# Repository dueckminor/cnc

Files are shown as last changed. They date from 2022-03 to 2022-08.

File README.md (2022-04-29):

# CNC-Mill

This is my first try to build a CNC-Mill

As a controller I use an ESP-32 with
[FluidNC](https://github.com/bdring/FluidNC)

I designed a PCB with the following features:
- 4 stepper motors (for the X1,X2,Y,Z axes)
- 1 spindle output (enable+pwm)
- 5 additional output pins
- 8 limit switches (5V powered), 2 for each axis
- 1 probe switch
- 3 additional input pins
- 1 SD-Card
- 1 I2C (for an OLED display)

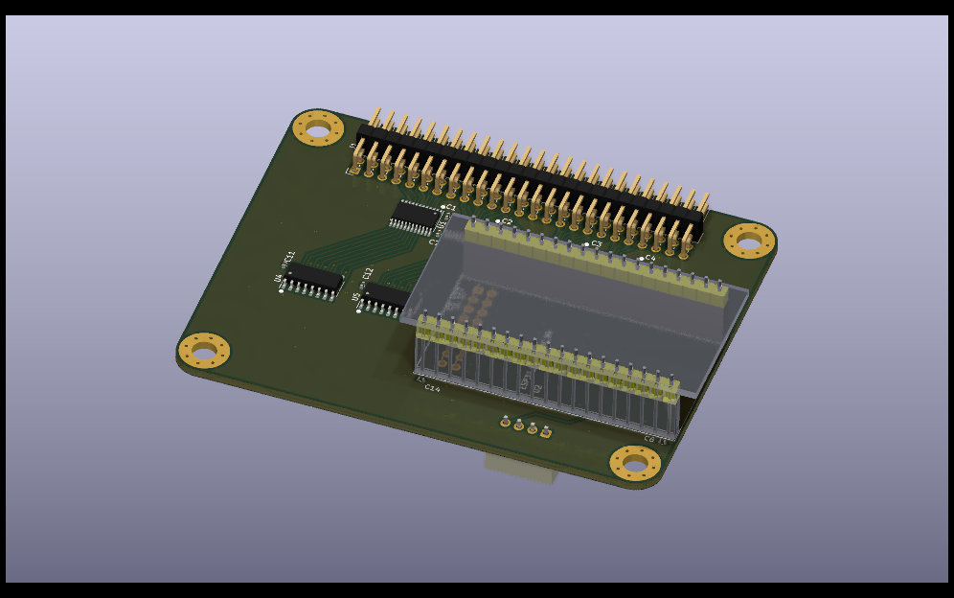
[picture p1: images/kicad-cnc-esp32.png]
esp32


This board gets connected using a 2x25 pin header to a connector-board
with many JST-XH connectors. This board contians also pull-up resistors
for each input switch (all inputs are active-low)

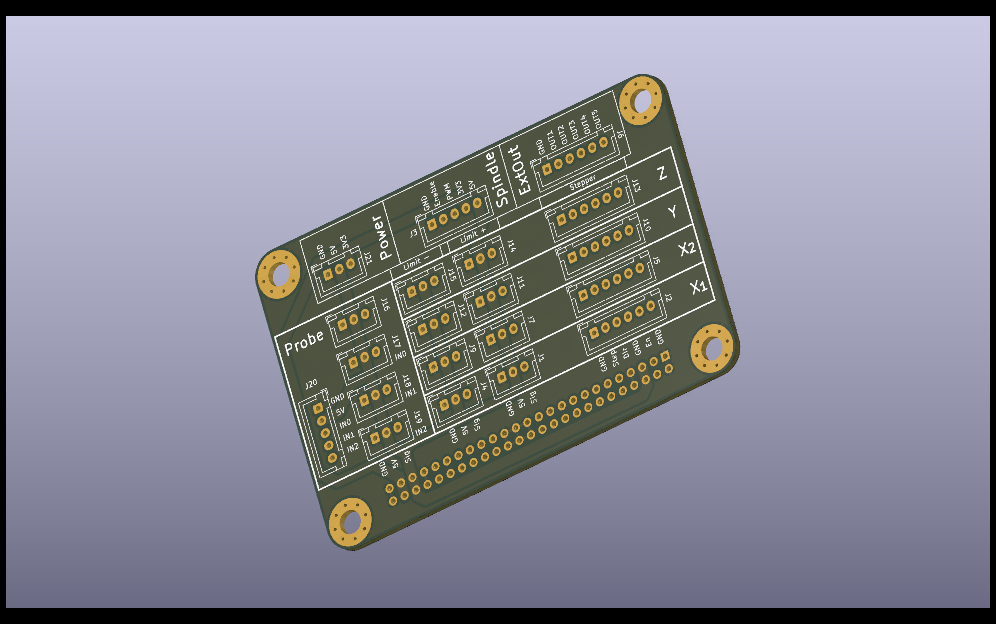
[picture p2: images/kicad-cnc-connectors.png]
connectors


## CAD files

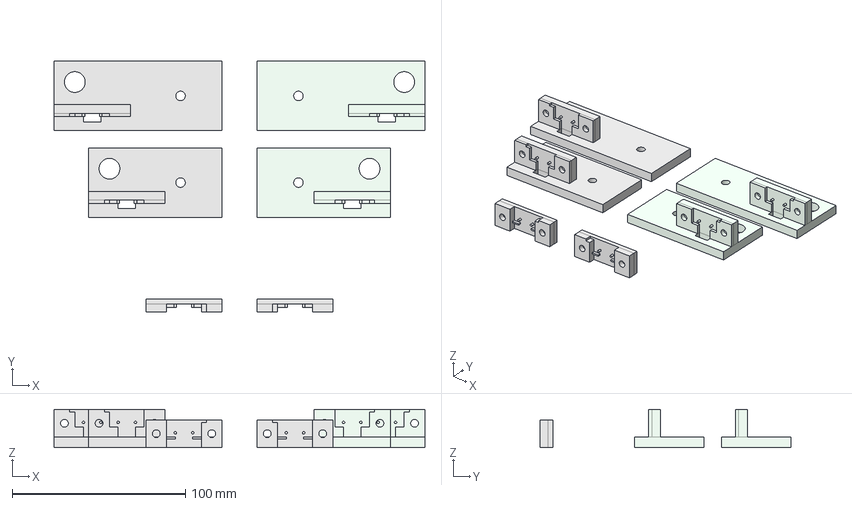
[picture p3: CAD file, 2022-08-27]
freecad/Endschalter-Halter.FCStd
214.0 x 144.5 x 22.0 mm
Halter-Kurz
Halter-Lang
Klemme
Halter-Kurz (Mirror #2)
Klemme (Mirror #3)
Halter-Lang (Mirror #3)

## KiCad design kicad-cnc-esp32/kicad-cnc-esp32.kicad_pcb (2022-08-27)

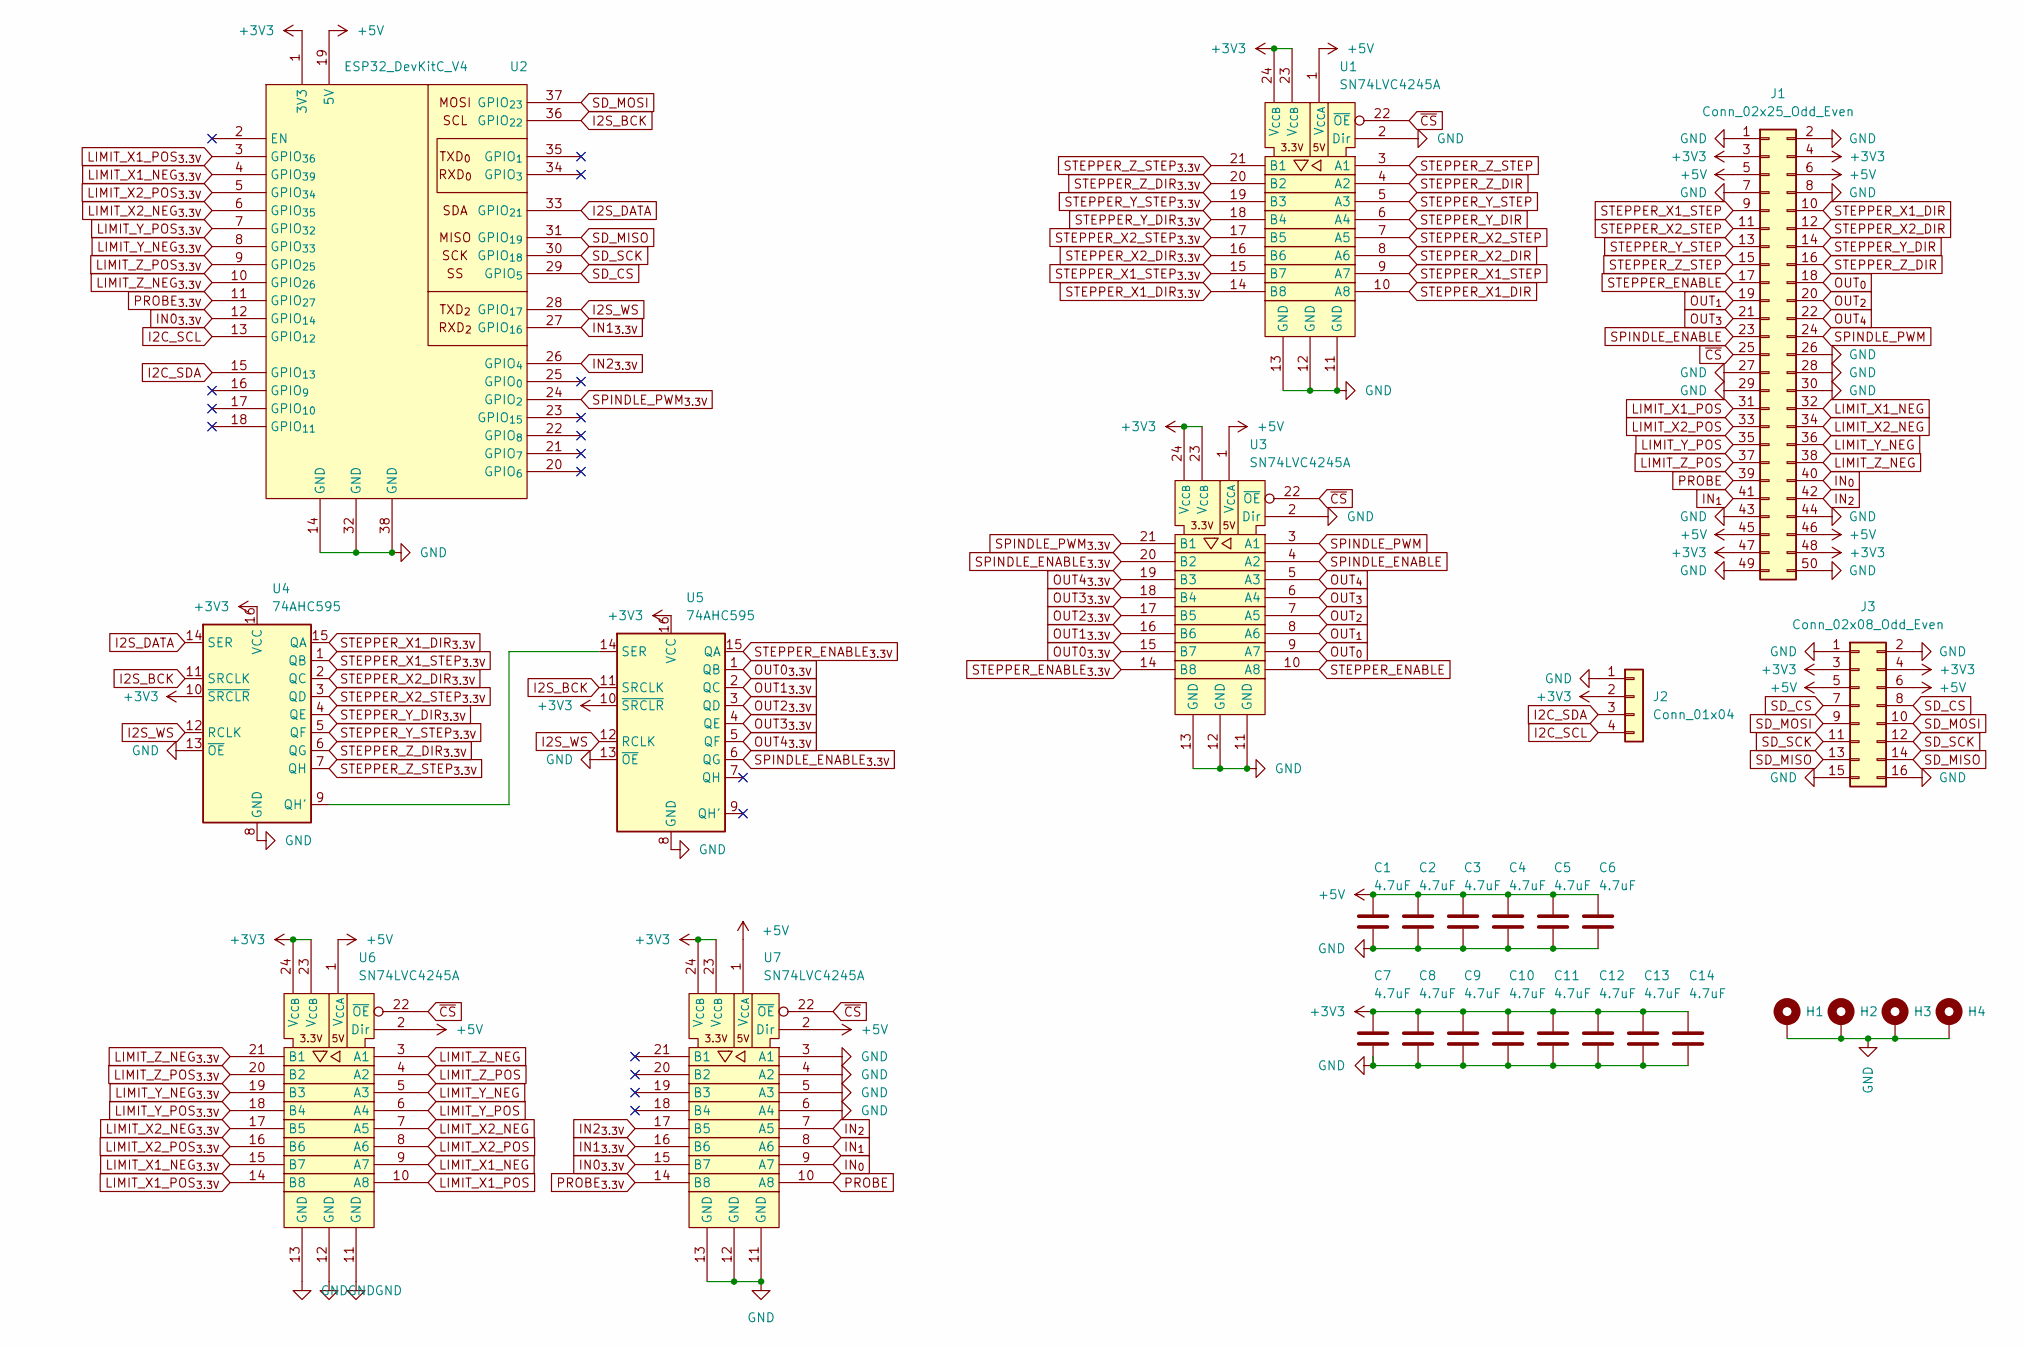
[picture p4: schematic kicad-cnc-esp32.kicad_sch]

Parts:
C1, C2, C3, C4, C5, C6, C7, C8, C9, C10, C11, C12, C13, C14: 4.7uF; C_0402_1005Metric; JLCPCB C23733
H1, H2, H3, H4: MountingHole_Pad; MountingHole_4.5mm_Pad_Via
J1: Conn_02x25_Odd_Even; PinHeader_2x25_P2.54mm_Horizontal
J2: Conn_01x04; JST_XH_B4B-XH-A_1x04_P2.50mm_Vertical
J3: Conn_02x08_Odd_Even; PinSocket_2x08_P2.54mm_Vertical
U1, U3, U6, U7: SN74LVC4245A; TSSOP-24_4.4x7.8mm_P0.65mm; JLCPCB C7859
U2: ESP32_DevKitC_V4
U4, U5: 74AHC595; SOIC-16_3.9x9.9mm_P1.27mm; JLCPCB C5947

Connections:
+3V3: C7.1, C8.1, C9.1, C10.1, C11.1, C12.1, C13.1, C14.1, J1.3, J1.4, J1.47, J1.48, J2.2, J3.3, J3.4, U1.23 (V_{CCB}), U1.24 (V_{CCB}), U2.1 (3V3), U3.23 (V_{CCB}), U3.24 (V_{CCB}), U4.10 (~SRCLR), U4.16 (VCC), U5.10 (~SRCLR), U5.16 (VCC), U6.23 (V_{CCB}), U6.24 (V_{CCB}), U7.23 (V_{CCB}), U7.24 (V_{CCB})
+5V: C1.1, C2.1, C3.1, C4.1, C5.1, C6.1, J1.5, J1.6, J1.45, J1.46, J3.5, J3.6, U1.1 (V_{CCA}), U2.19 (5V), U3.1 (V_{CCA}), U6.1 (V_{CCA}), U6.2 (Dir), U7.1 (V_{CCA}), U7.2 (Dir)
GND: C1.2, C2.2, C3.2, C4.2, C5.2, C6.2, C7.2, C8.2, C9.2, C10.2, C11.2, C12.2, C13.2, C14.2, H1.1, H2.1, H3.1, H4.1, J1.1, J1.2, J1.7, J1.8, J1.26, J1.27, J1.28, J1.29, J1.30, J1.43, J1.44, J1.49, J1.50, J2.1, J3.1, J3.2, J3.15, J3.16, U1.2 (Dir), U1.11 (GND), U1.12 (GND), U1.13 (GND), U2.14 (GND), U2.32 (GND), U2.38 (GND), U3.2 (Dir), U3.11 (GND), U3.12 (GND), U3.13 (GND), U4.8 (GND), U4.13 (~OE), U5.8 (GND), U5.13 (~OE), U6.11 (GND), U6.12 (GND), U6.13 (GND), U7.3 (A1), U7.4 (A2), U7.5 (A3), U7.6 (A4), U7.11 (GND), U7.12 (GND), U7.13 (GND)
I2C_SCL: J2.4, U2.13 (GPIO_{12})
I2C_SDA: J2.3, U2.15 (GPIO_{13})
I2S_BCK: U2.36 (GPIO_{22}), U4.11 (SRCLK), U5.11 (SRCLK)
I2S_DATA: U2.33 (GPIO_{21}), U4.14 (SER)
I2S_WS: U2.28 (GPIO_{17}), U4.12 (RCLK), U5.12 (RCLK)
IN0_{3.3V}: U2.12 (GPIO_{14}), U7.15 (B7)
IN1_{3.3V}: U2.27 (GPIO_{16}), U7.16 (B6)
IN2_{3.3V}: U2.26 (GPIO_{4}), U7.17 (B5)
IN_{0}: J1.40, U7.9 (A7)
IN_{1}: J1.41, U7.8 (A6)
IN_{2}: J1.42, U7.7 (A5)
LIMIT_X1_NEG: J1.32, U6.9 (A7)
LIMIT_X1_NEG_{3.3V}: U2.4 (GPIO_{39}), U6.15 (B7)
LIMIT_X1_POS: J1.31, U6.10 (A8)
LIMIT_X1_POS_{3.3V}: U2.3 (GPIO_{36}), U6.14 (B8)
LIMIT_X2_NEG: J1.34, U6.7 (A5)
LIMIT_X2_NEG_{3.3V}: U2.6 (GPIO_{35}), U6.17 (B5)
LIMIT_X2_POS: J1.33, U6.8 (A6)
LIMIT_X2_POS_{3.3V}: U2.5 (GPIO_{34}), U6.16 (B6)
LIMIT_Y_NEG: J1.36, U6.5 (A3)
LIMIT_Y_NEG_{3.3V}: U2.8 (GPIO_{33}), U6.19 (B3)
LIMIT_Y_POS: J1.35, U6.6 (A4)
LIMIT_Y_POS_{3.3V}: U2.7 (GPIO_{32}), U6.18 (B4)
LIMIT_Z_NEG: J1.38, U6.3 (A1)
LIMIT_Z_NEG_{3.3V}: U2.10 (GPIO_{26}), U6.21 (B1)
LIMIT_Z_POS: J1.37, U6.4 (A2)
LIMIT_Z_POS_{3.3V}: U2.9 (GPIO_{25}), U6.20 (B2)
unnamed: U4.9 (QH'), U5.14 (SER)
OUT0_{3.3V}: U3.15 (B7), U5.1 (QB)
OUT1_{3.3V}: U3.16 (B6), U5.2 (QC)
OUT2_{3.3V}: U3.17 (B5), U5.3 (QD)
OUT3_{3.3V}: U3.18 (B4), U5.4 (QE)
OUT4_{3.3V}: U3.19 (B3), U5.5 (QF)
OUT_{0}: J1.18, U3.9 (A7)
OUT_{1}: J1.19, U3.8 (A6)
OUT_{2}: J1.20, U3.7 (A5)
OUT_{3}: J1.21, U3.6 (A4)
OUT_{4}: J1.22, U3.5 (A3)
PROBE: J1.39, U7.10 (A8)
PROBE_{3.3V}: U2.11 (GPIO_{27}), U7.14 (B8)
SD_CS: J3.7, J3.8, U2.29 (GPIO_{5})
SD_MISO: J3.13, J3.14, U2.31 (GPIO_{19})
SD_MOSI: J3.9, J3.10, U2.37 (GPIO_{23})
SD_SCK: J3.11, J3.12, U2.30 (GPIO_{18})
SPINDLE_ENABLE: J1.23, U3.4 (A2)
SPINDLE_ENABLE_{3.3V}: U3.20 (B2), U5.6 (QG)
SPINDLE_PWM: J1.24, U3.3 (A1)
SPINDLE_PWM_{3.3V}: U2.24 (GPIO_{2}), U3.21 (B1)
STEPPER_ENABLE: J1.17, U3.10 (A8)
STEPPER_ENABLE_{3.3V}: U3.14 (B8), U5.15 (QA)
STEPPER_X1_DIR: J1.10, U1.10 (A8)
STEPPER_X1_DIR_{3.3V}: U1.14 (B8), U4.15 (QA)
STEPPER_X1_STEP: J1.9, U1.9 (A7)
STEPPER_X1_STEP_{3.3V}: U1.15 (B7), U4.1 (QB)
STEPPER_X2_DIR: J1.12, U1.8 (A6)
STEPPER_X2_DIR_{3.3V}: U1.16 (B6), U4.2 (QC)
STEPPER_X2_STEP: J1.11, U1.7 (A5)
STEPPER_X2_STEP_{3.3V}: U1.17 (B5), U4.3 (QD)
STEPPER_Y_DIR: J1.14, U1.6 (A4)
STEPPER_Y_DIR_{3.3V}: U1.18 (B4), U4.4 (QE)
STEPPER_Y_STEP: J1.13, U1.5 (A3)
STEPPER_Y_STEP_{3.3V}: U1.19 (B3), U4.5 (QF)
STEPPER_Z_DIR: J1.16, U1.4 (A2)
STEPPER_Z_DIR_{3.3V}: U1.20 (B2), U4.6 (QG)
STEPPER_Z_STEP: J1.15, U1.3 (A1)
STEPPER_Z_STEP_{3.3V}: U1.21 (B1), U4.7 (QH)
~CS: J1.25, U1.22 (~OE), U3.22 (~OE), U6.22 (~OE), U7.22 (~OE)

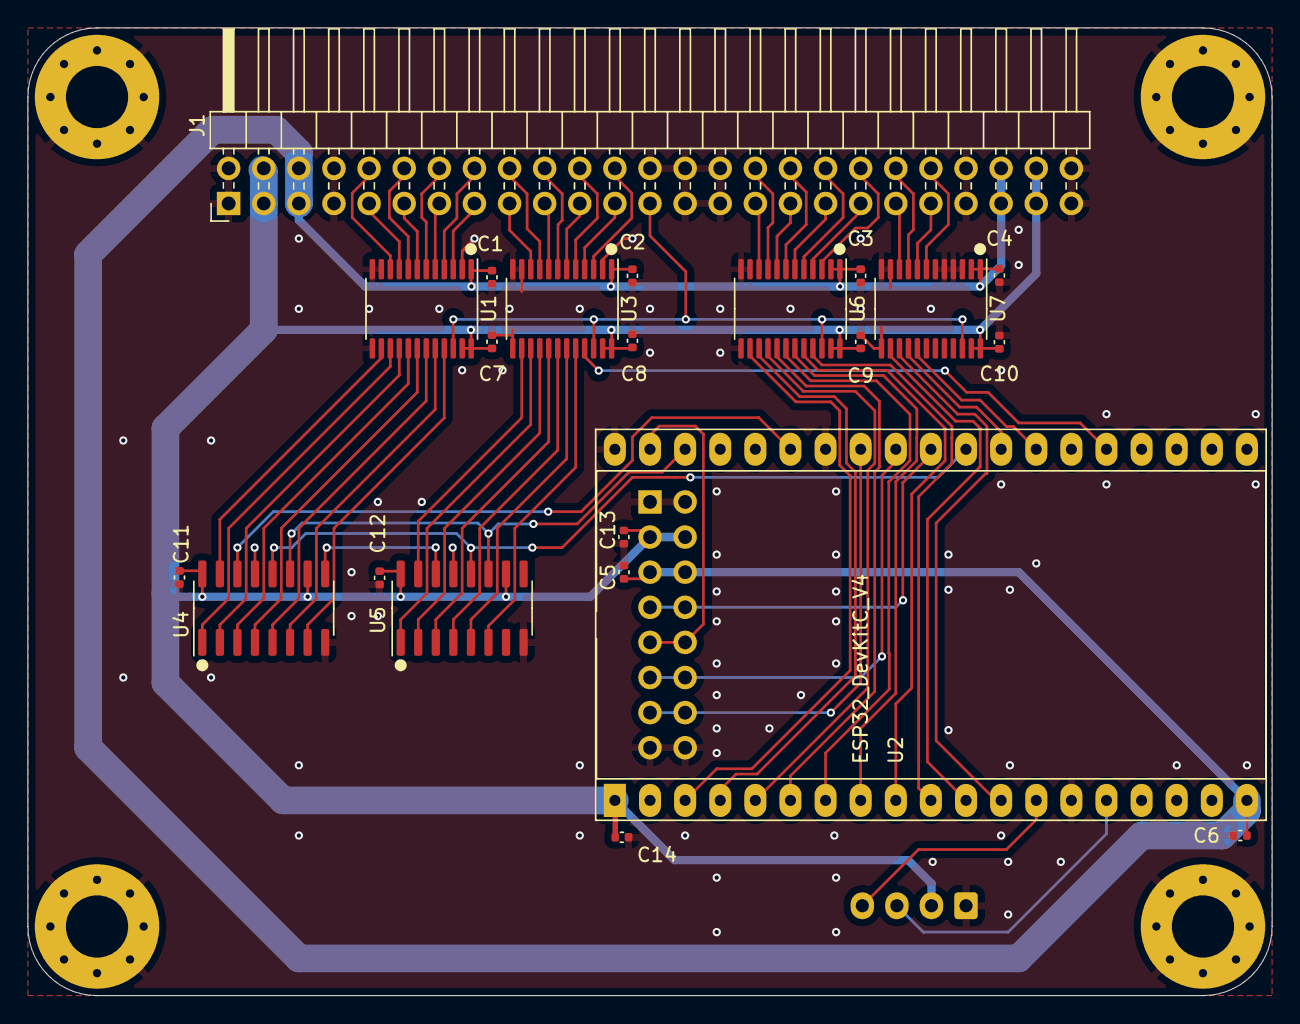
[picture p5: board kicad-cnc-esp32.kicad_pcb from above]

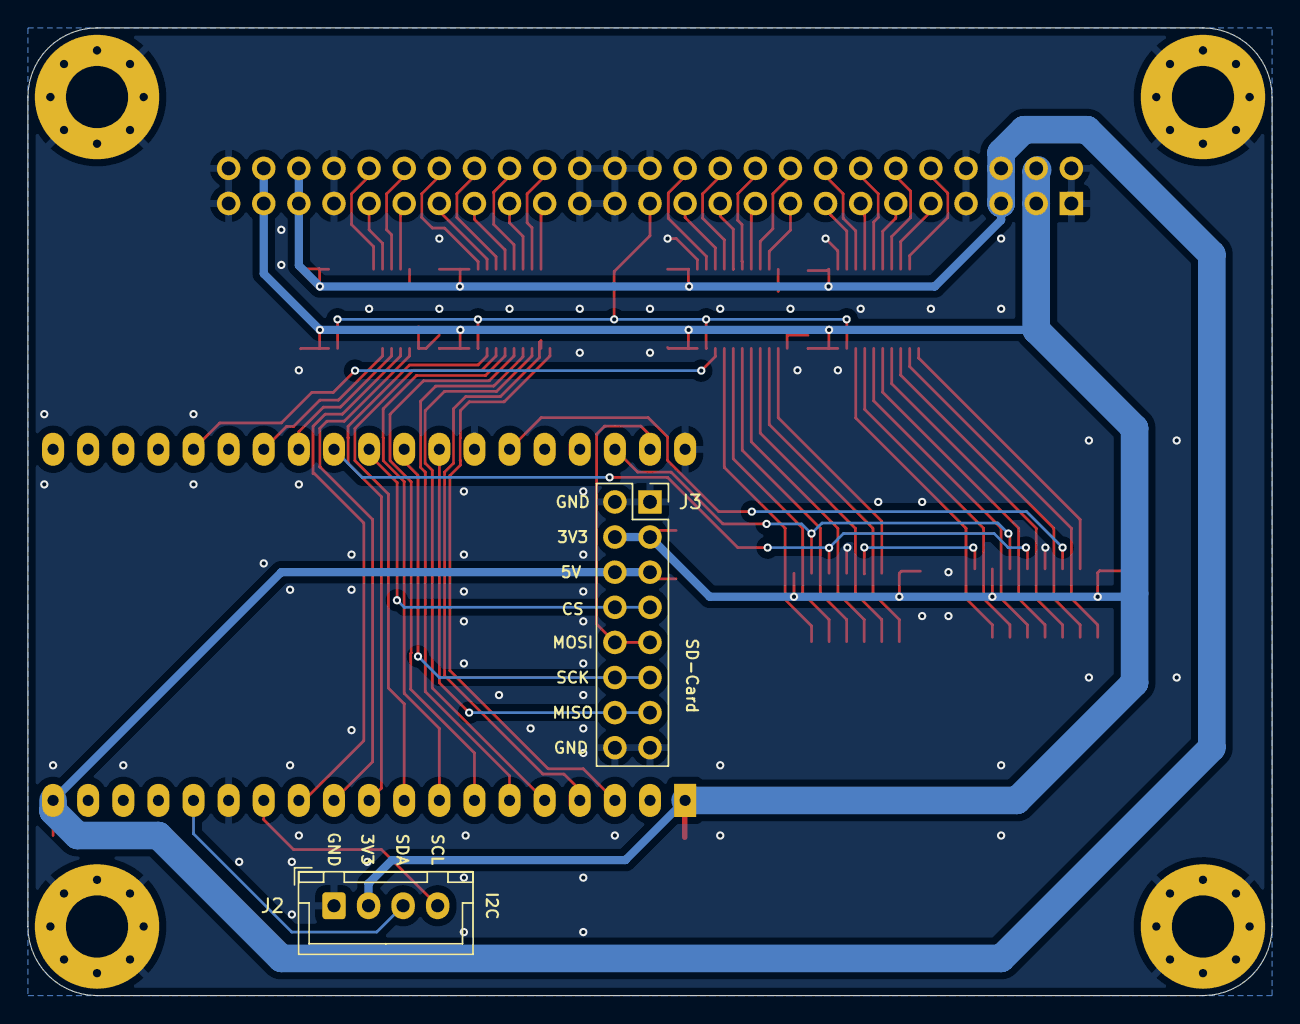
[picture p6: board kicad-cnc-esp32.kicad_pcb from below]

Board: 2 copper layers, 90.0 x 70.0 mm, 28 parts (2 on the bottom side), 70 nets.

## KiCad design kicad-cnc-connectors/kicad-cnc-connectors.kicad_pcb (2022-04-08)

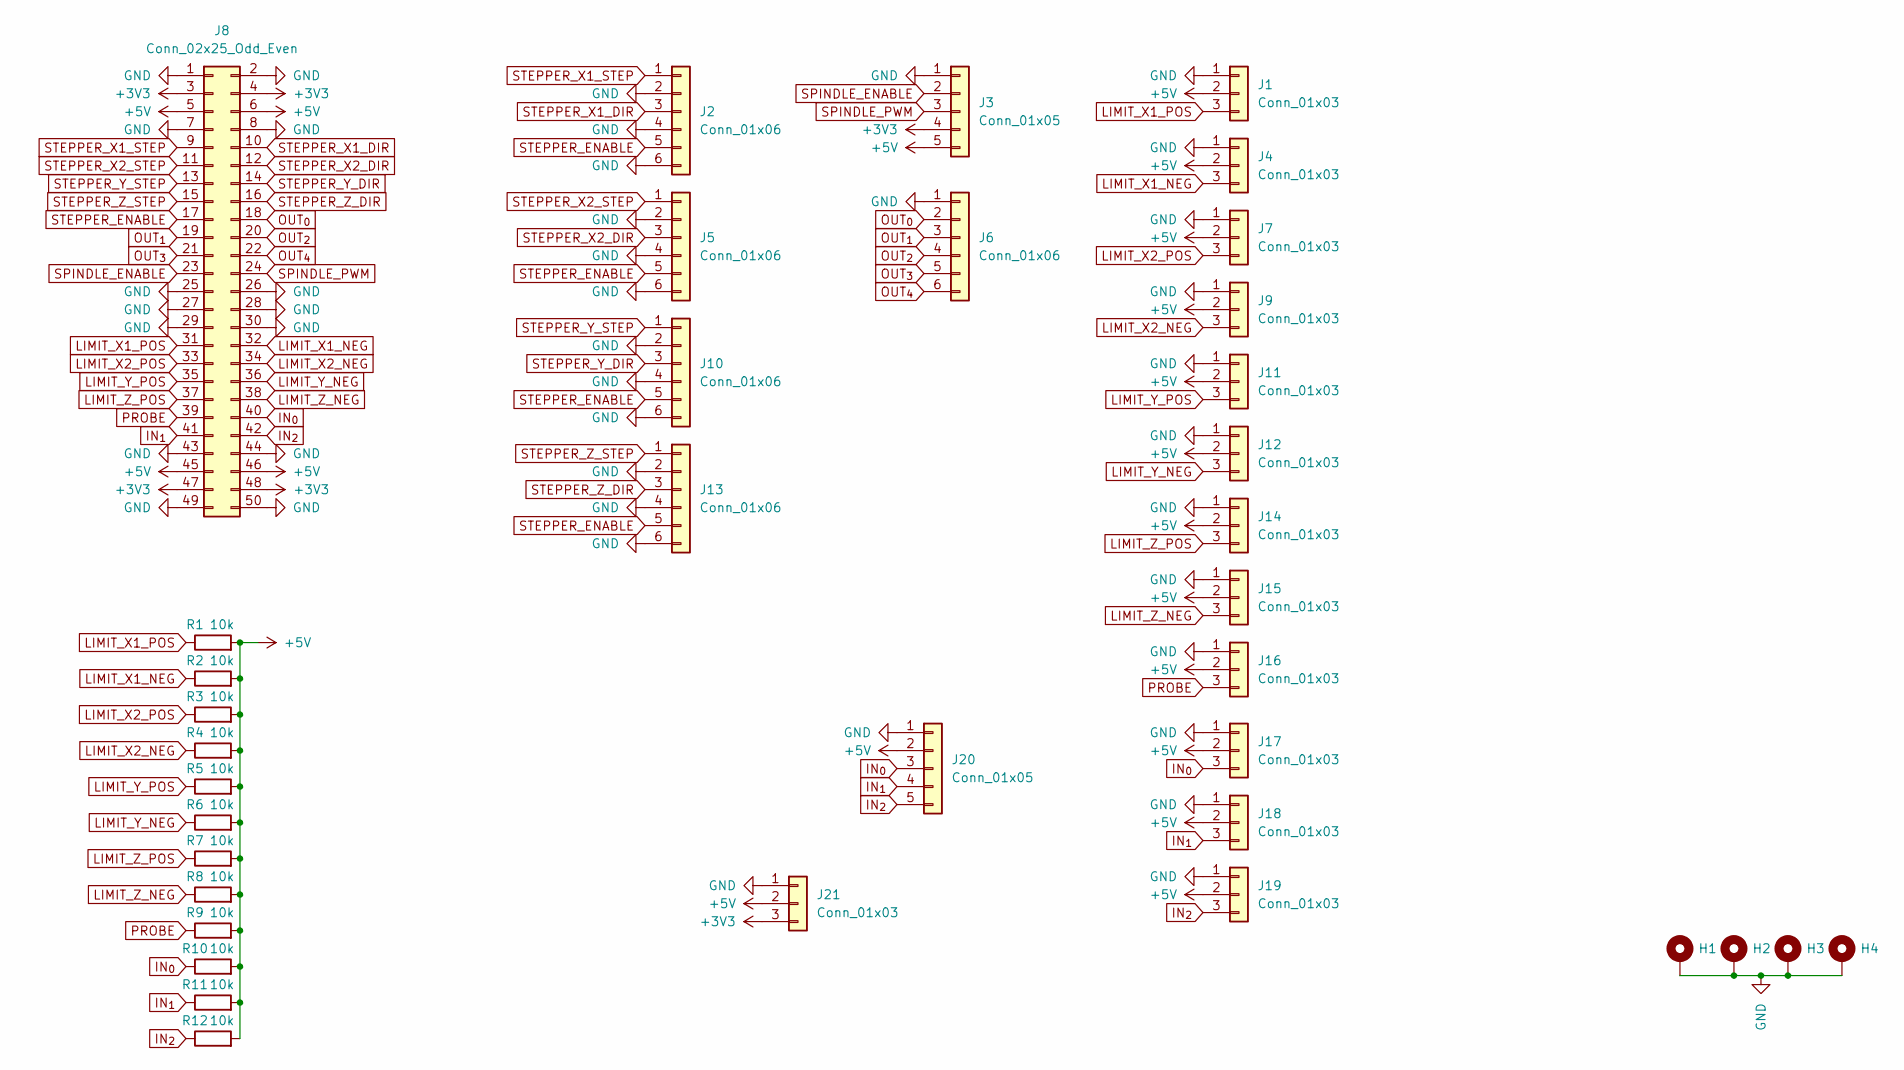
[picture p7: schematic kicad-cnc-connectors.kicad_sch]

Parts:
H1, H2, H3, H4: MountingHole_Pad; MountingHole_4.5mm_Pad_Via
J1, J4, J7, J9, J11, J12, J14, J15, J16, J17, J18, J19, J21: Conn_01x03; JST_XH_B3B-XH-A_1x03_P2.50mm_Vertical
J2, J5, J6, J10, J13: Conn_01x06; JST_XH_B6B-XH-A_1x06_P2.50mm_Vertical
J3, J20: Conn_01x05; JST_XH_B5B-XH-A_1x05_P2.50mm_Vertical
J8: Conn_02x25_Odd_Even; PinSocket_2x25_P2.54mm_Vertical
R1, R2, R3, R4, R5, R6, R7, R8, R9, R10, R11, R12: 10k; R_0402_1005Metric

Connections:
+3V3: J3.4, J8.3, J8.4, J8.47, J8.48, J21.3
+5V: J1.2, J3.5, J4.2, J7.2, J8.5, J8.6, J8.45, J8.46, J9.2, J11.2, J12.2, J14.2, J15.2, J16.2, J17.2, J18.2, J19.2, J20.2, J21.2, R1.2, R2.2, R3.2, R4.2, R5.2, R6.2, R7.2, R8.2, R9.2, R10.2, R11.2, R12.2
GND: H1.1, H2.1, H3.1, H4.1, J1.1, J2.2, J2.4, J2.6, J3.1, J4.1, J5.2, J5.4, J5.6, J6.1, J7.1, J8.1, J8.2, J8.7, J8.8, J8.25, J8.26, J8.27, J8.28, J8.29, J8.30, J8.43, J8.44, J8.49, J8.50, J9.1, J10.2, J10.4, J10.6, J11.1, J12.1, J13.2, J13.4, J13.6, J14.1, J15.1, J16.1, J17.1, J18.1, J19.1, J20.1, J21.1
IN_{0}: J8.40, J17.3, J20.3, R10.1
IN_{1}: J8.41, J18.3, J20.4, R11.1
IN_{2}: J8.42, J19.3, J20.5, R12.1
LIMIT_X1_NEG: J4.3, J8.32, R2.1
LIMIT_X1_POS: J1.3, J8.31, R1.1
LIMIT_X2_NEG: J8.34, J9.3, R4.1
LIMIT_X2_POS: J7.3, J8.33, R3.1
LIMIT_Y_NEG: J8.36, J12.3, R6.1
LIMIT_Y_POS: J8.35, J11.3, R5.1
LIMIT_Z_NEG: J8.38, J15.3, R8.1
LIMIT_Z_POS: J8.37, J14.3, R7.1
OUT_{0}: J6.2, J8.18
OUT_{1}: J6.3, J8.19
OUT_{2}: J6.4, J8.20
OUT_{3}: J6.5, J8.21
OUT_{4}: J6.6, J8.22
PROBE: J8.39, J16.3, R9.1
SPINDLE_ENABLE: J3.2, J8.23
SPINDLE_PWM: J3.3, J8.24
STEPPER_ENABLE: J2.5, J5.5, J8.17, J10.5, J13.5
STEPPER_X1_DIR: J2.3, J8.10
STEPPER_X1_STEP: J2.1, J8.9
STEPPER_X2_DIR: J5.3, J8.12
STEPPER_X2_STEP: J5.1, J8.11
STEPPER_Y_DIR: J8.14, J10.3
STEPPER_Y_STEP: J8.13, J10.1
STEPPER_Z_DIR: J8.16, J13.3
STEPPER_Z_STEP: J8.15, J13.1

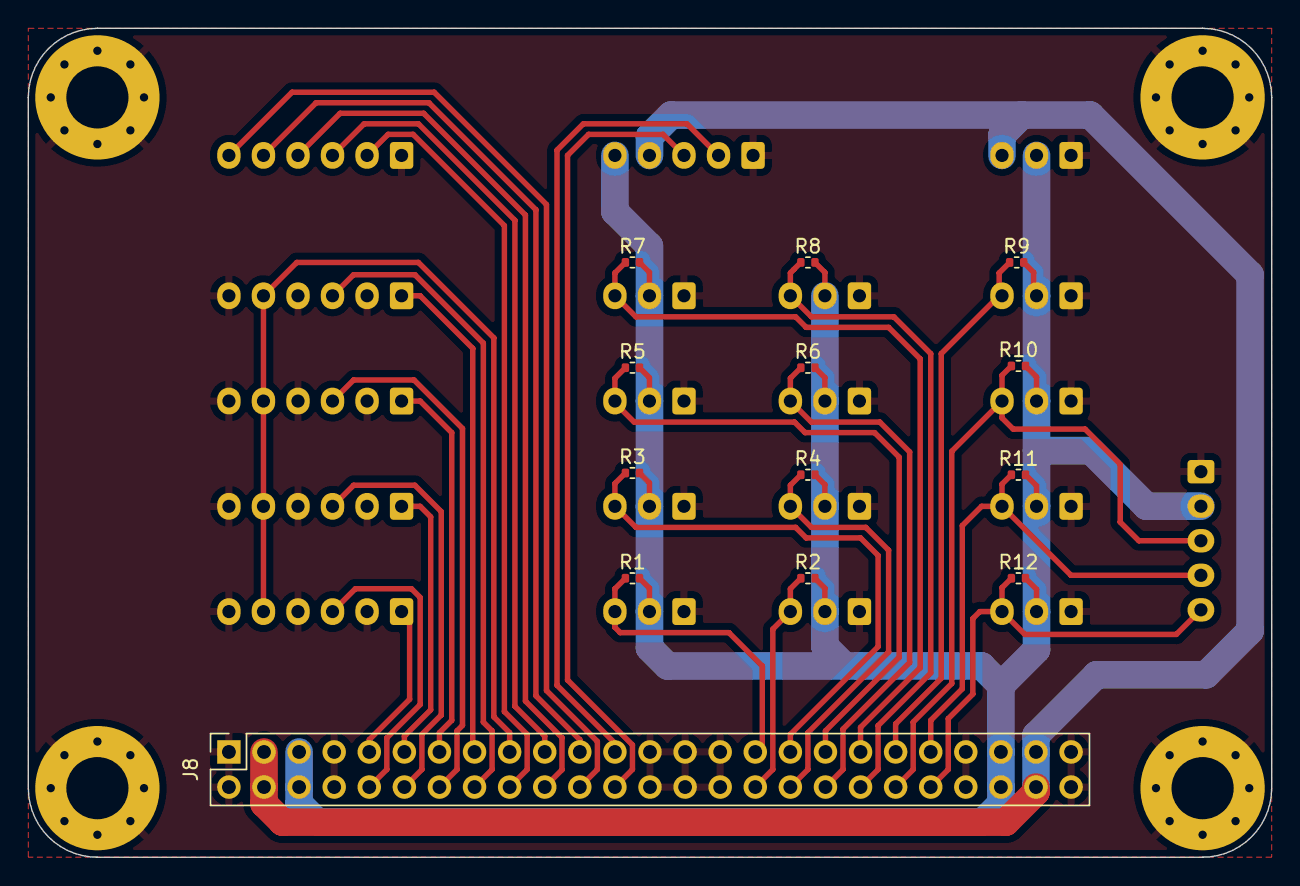
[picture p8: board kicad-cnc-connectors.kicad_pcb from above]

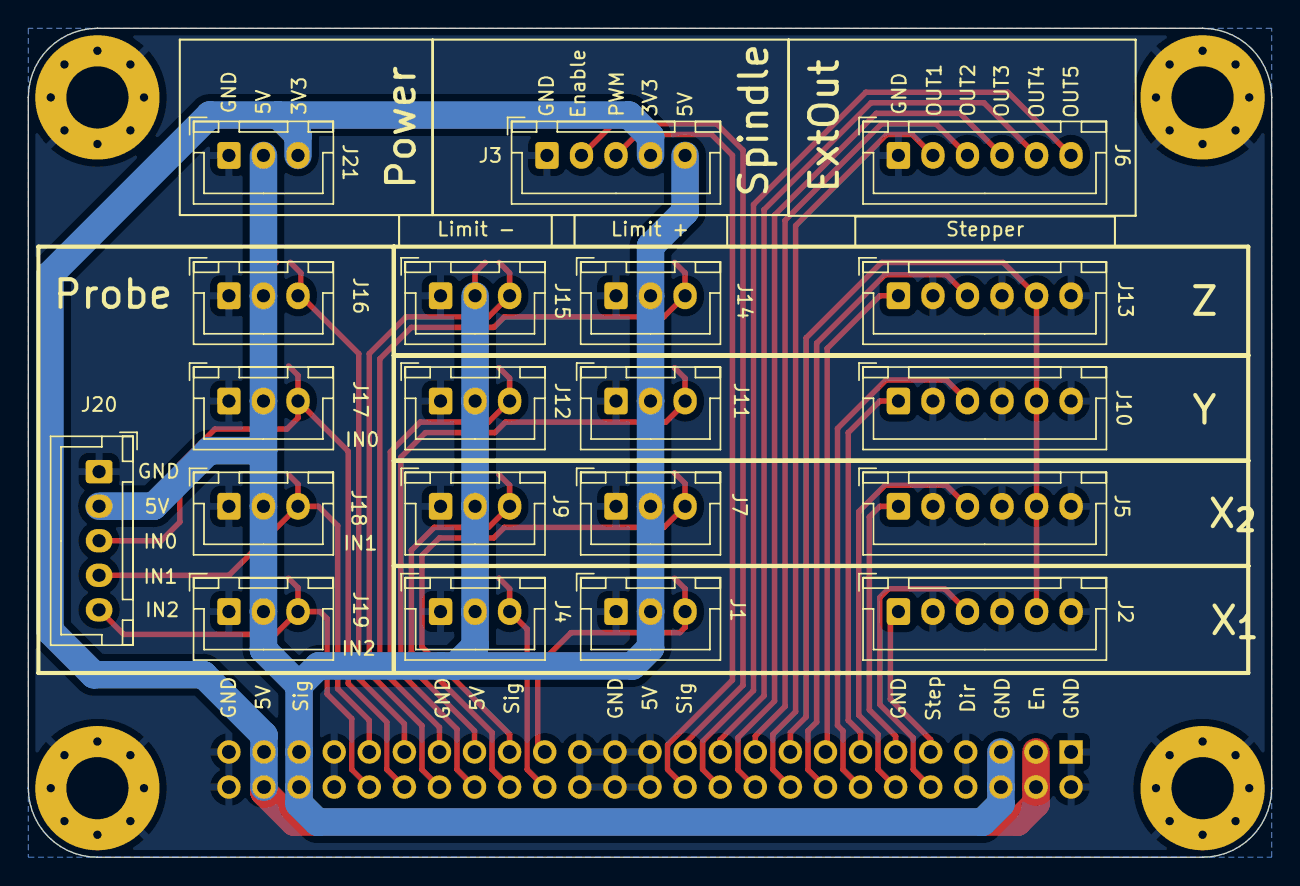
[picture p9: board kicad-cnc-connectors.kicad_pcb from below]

Board: 2 copper layers, 90.0 x 60.0 mm, 37 parts (20 on the bottom side), 31 nets.

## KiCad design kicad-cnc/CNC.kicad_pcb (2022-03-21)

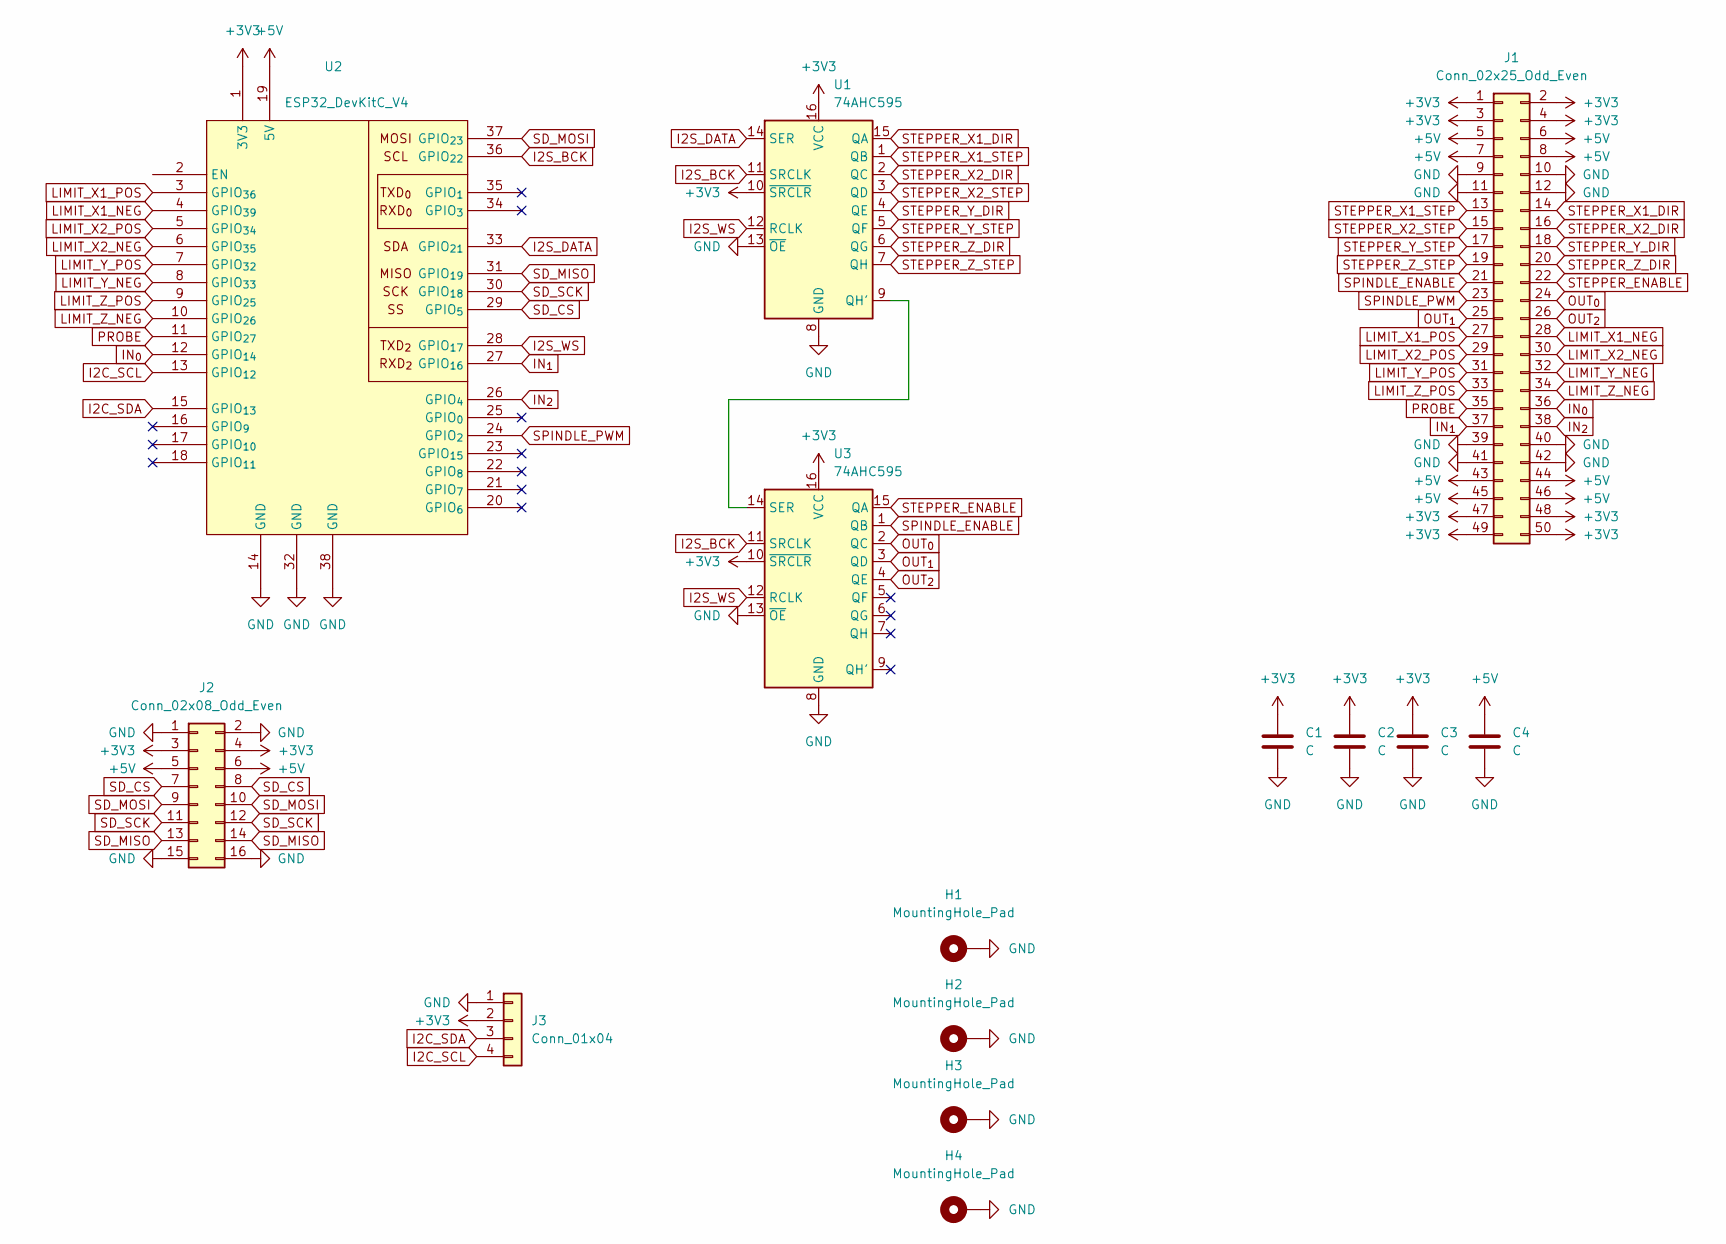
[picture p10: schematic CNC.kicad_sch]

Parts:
C1, C2, C3, C4: C; C_0402_1005Metric
H1, H2, H3, H4: MountingHole_Pad; MountingHole_4.5mm_Pad_Via
J1: Conn_02x25_Odd_Even; PinHeader_2x25_P2.54mm_Horizontal
J2: Conn_02x08_Odd_Even; PinSocket_2x08_P2.54mm_Vertical
J3: Conn_01x04; JST_XH_B4B-XH-A_1x04_P2.50mm_Vertical
U1, U3: 74AHC595; SOIC-16_3.9x9.9mm_P1.27mm
U2: ESP32_DevKitC_V4

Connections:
+3V3: C1.1, C2.1, C3.1, J1.1, J1.2, J1.3, J1.4, J1.47, J1.48, J1.49, J1.50, J2.3, J2.4, J3.2, U1.10 (~SRCLR), U1.16 (VCC), U2.1 (3V3), U3.10 (~SRCLR), U3.16 (VCC)
+5V: C4.1, J1.5, J1.6, J1.7, J1.8, J1.43, J1.44, J1.45, J1.46, J2.5, J2.6, U2.19 (5V)
GND: C1.2, C2.2, C3.2, C4.2, H1.1, H2.1, H3.1, H4.1, J1.9, J1.10, J1.11, J1.12, J1.39, J1.40, J1.41, J1.42, J2.1, J2.2, J2.15, J2.16, J3.1, U1.8 (GND), U1.13 (~OE), U2.14 (GND), U2.32 (GND), U2.38 (GND), U3.8 (GND), U3.13 (~OE)
I2C_SCL: J3.4, U2.13 (GPIO_{12})
I2C_SDA: J3.3, U2.15 (GPIO_{13})
I2S_BCK: U1.11 (SRCLK), U2.36 (GPIO_{22}), U3.11 (SRCLK)
I2S_DATA: U1.14 (SER), U2.33 (GPIO_{21})
I2S_WS: U1.12 (RCLK), U2.28 (GPIO_{17}), U3.12 (RCLK)
IN_{0}: J1.36, U2.12 (GPIO_{14})
IN_{1}: J1.37, U2.27 (GPIO_{16})
IN_{2}: J1.38, U2.26 (GPIO_{4})
LIMIT_X1_NEG: J1.28, U2.4 (GPIO_{39})
LIMIT_X1_POS: J1.27, U2.3 (GPIO_{36})
LIMIT_X2_NEG: J1.30, U2.6 (GPIO_{35})
LIMIT_X2_POS: J1.29, U2.5 (GPIO_{34})
LIMIT_Y_NEG: J1.32, U2.8 (GPIO_{33})
LIMIT_Y_POS: J1.31, U2.7 (GPIO_{32})
LIMIT_Z_NEG: J1.34, U2.10 (GPIO_{26})
LIMIT_Z_POS: J1.33, U2.9 (GPIO_{25})
unnamed: U1.9 (QH'), U3.14 (SER)
OUT_{0}: J1.24, U3.2 (QC)
OUT_{1}: J1.25, U3.3 (QD)
OUT_{2}: J1.26, U3.4 (QE)
PROBE: J1.35, U2.11 (GPIO_{27})
SD_CS: J2.7, J2.8, U2.29 (GPIO_{5})
SD_MISO: J2.13, J2.14, U2.31 (GPIO_{19})
SD_MOSI: J2.9, J2.10, U2.37 (GPIO_{23})
SD_SCK: J2.11, J2.12, U2.30 (GPIO_{18})
SPINDLE_ENABLE: J1.21, U3.1 (QB)
SPINDLE_PWM: J1.23, U2.24 (GPIO_{2})
STEPPER_ENABLE: J1.22, U3.15 (QA)
STEPPER_X1_DIR: J1.14, U1.15 (QA)
STEPPER_X1_STEP: J1.13, U1.1 (QB)
STEPPER_X2_DIR: J1.16, U1.2 (QC)
STEPPER_X2_STEP: J1.15, U1.3 (QD)
STEPPER_Y_DIR: J1.18, U1.4 (QE)
STEPPER_Y_STEP: J1.17, U1.5 (QF)
STEPPER_Z_DIR: J1.20, U1.6 (QG)
STEPPER_Z_STEP: J1.19, U1.7 (QH)

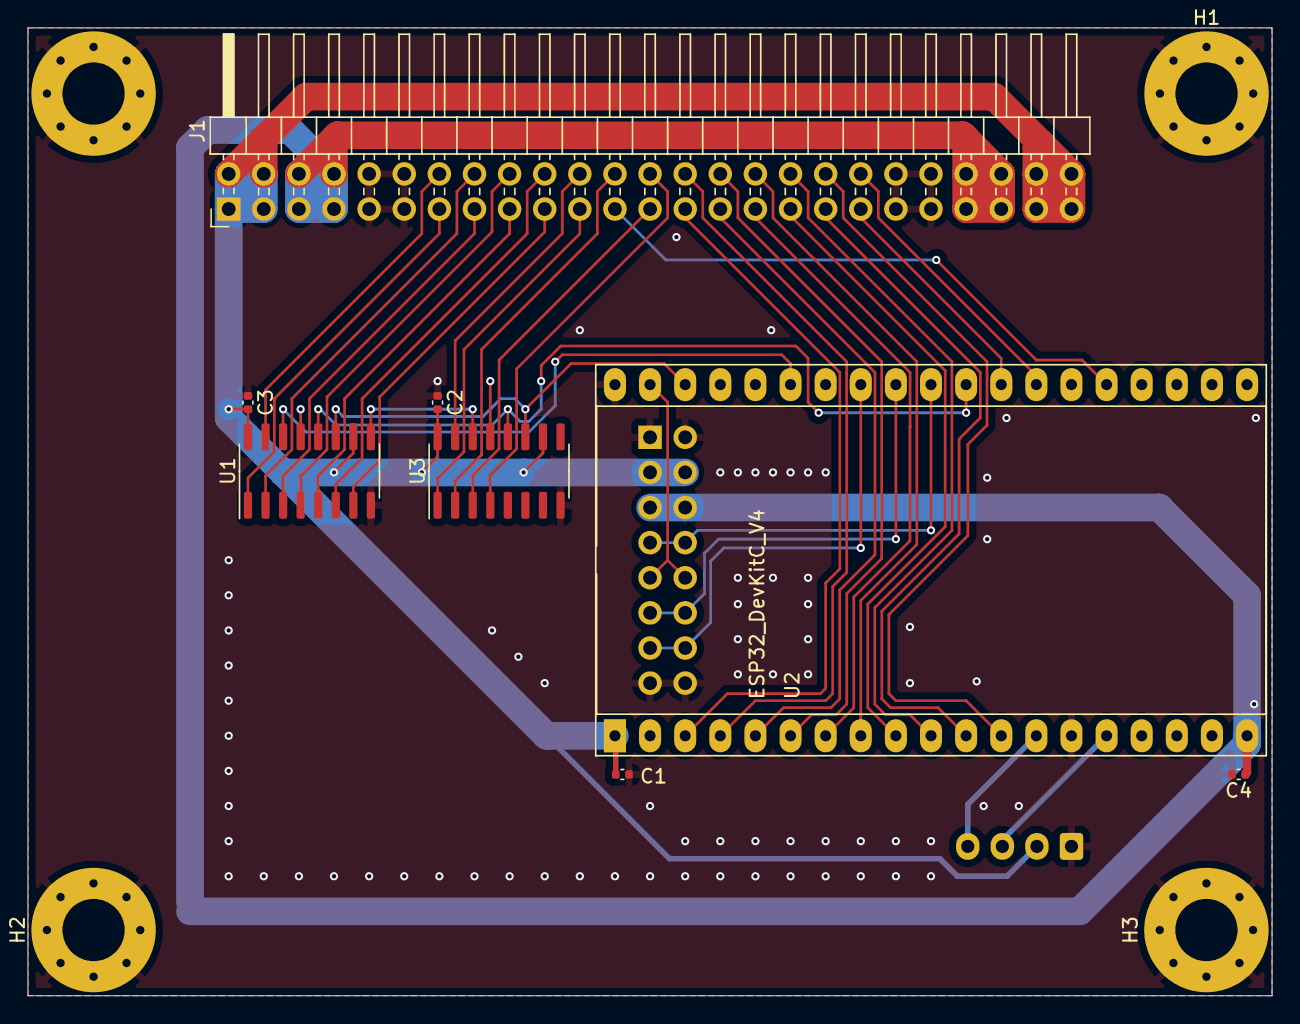
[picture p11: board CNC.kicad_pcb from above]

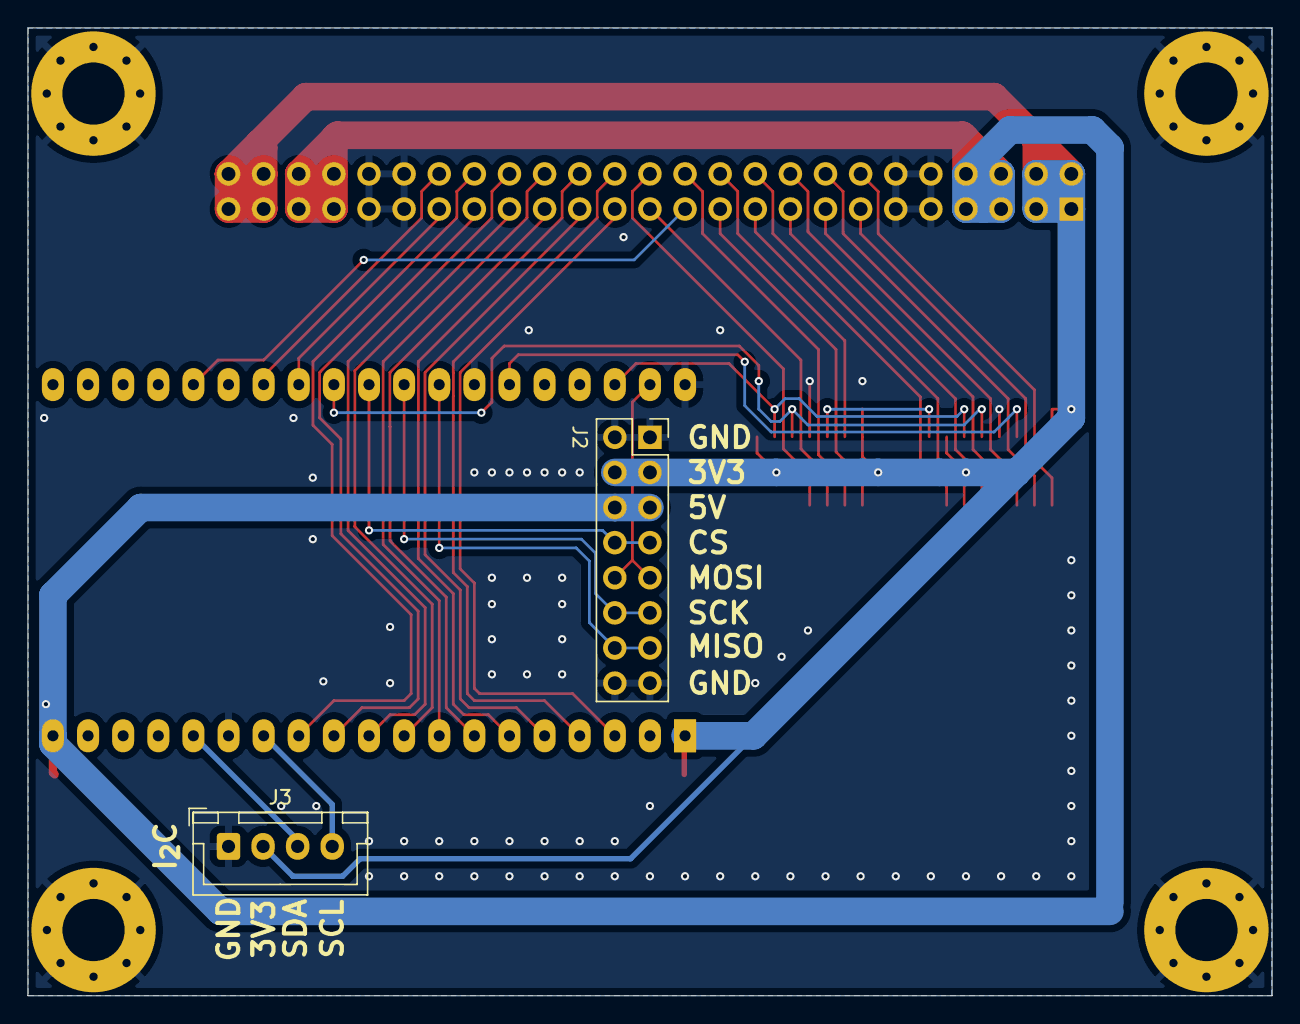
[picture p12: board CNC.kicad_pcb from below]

Board: 4 copper layers, 90.0 x 70.0 mm, 14 parts (2 on the bottom side), 39 nets.

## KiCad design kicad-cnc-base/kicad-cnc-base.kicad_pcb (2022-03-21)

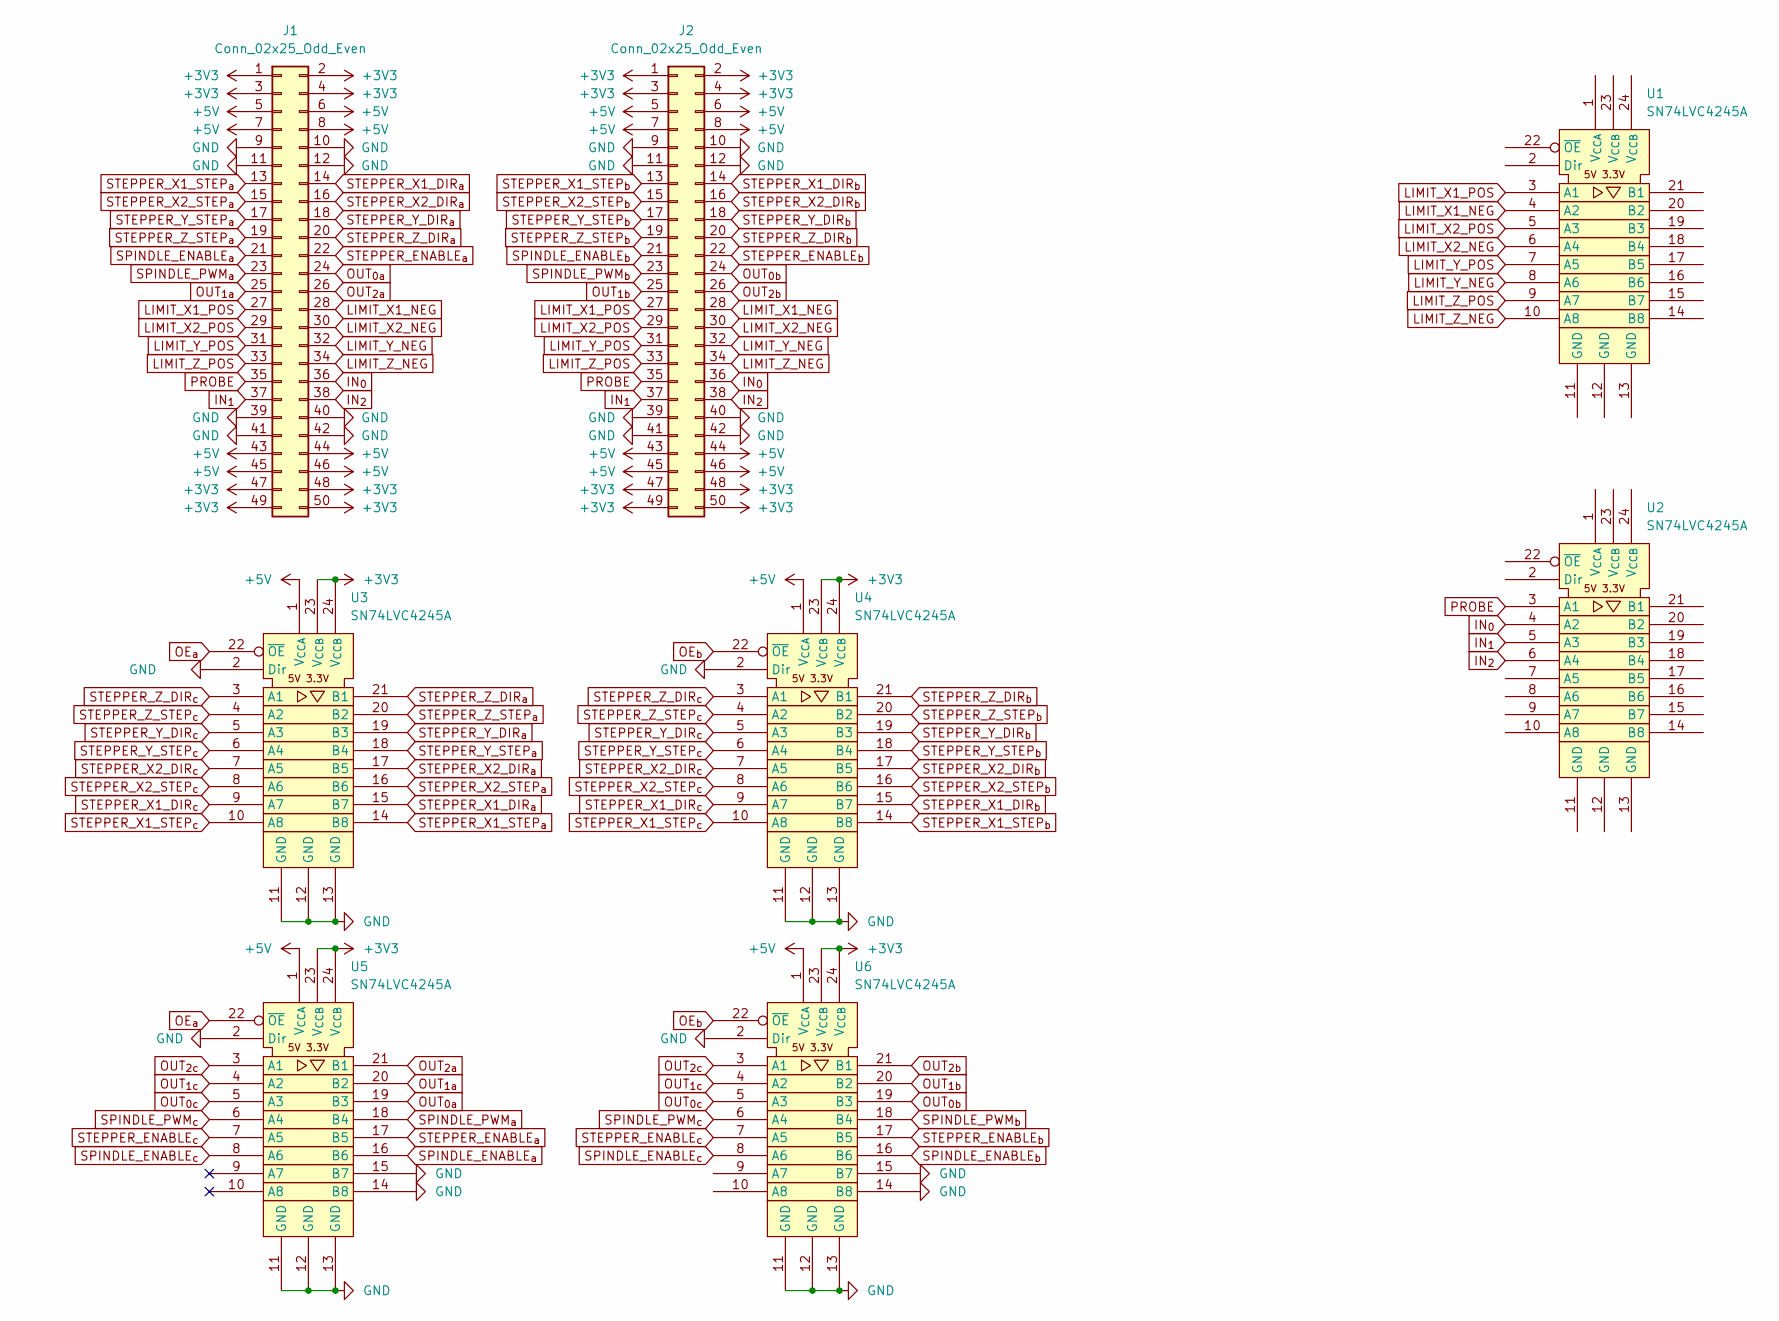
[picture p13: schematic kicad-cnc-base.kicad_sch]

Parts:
J1, J2: Conn_02x25_Odd_Even; PinSocket_2x25_P2.54mm_Vertical
U1, U2, U3, U4, U5, U6: SN74LVC4245A; TSSOP-24_4.4x7.8mm_P0.65mm

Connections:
+3V3: J1.1, J1.2, J1.3, J1.4, J1.47, J1.48, J1.49, J1.50, J2.1, J2.2, J2.3, J2.4, J2.47, J2.48, J2.49, J2.50, U3.23 (V_{CCB}), U3.24 (V_{CCB}), U4.23 (V_{CCB}), U4.24 (V_{CCB}), U5.23 (V_{CCB}), U5.24 (V_{CCB}), U6.23 (V_{CCB}), U6.24 (V_{CCB})
+5V: J1.5, J1.6, J1.7, J1.8, J1.43, J1.44, J1.45, J1.46, J2.5, J2.6, J2.7, J2.8, J2.43, J2.44, J2.45, J2.46, U3.1 (V_{CCA}), U4.1 (V_{CCA}), U5.1 (V_{CCA}), U6.1 (V_{CCA})
GND: J1.9, J1.10, J1.11, J1.12, J1.39, J1.40, J1.41, J1.42, J2.9, J2.10, J2.11, J2.12, J2.39, J2.40, J2.41, J2.42, U3.2 (Dir), U3.11 (GND), U3.12 (GND), U3.13 (GND), U4.2 (Dir), U4.11 (GND), U4.12 (GND), U4.13 (GND), U5.2 (Dir), U5.11 (GND), U5.12 (GND), U5.13 (GND), U5.14 (B8), U5.15 (B7), U6.2 (Dir), U6.11 (GND), U6.12 (GND), U6.13 (GND), U6.14 (B8), U6.15 (B7)
IN_{0}: J1.36, J2.36, U2.4 (A2)
IN_{1}: J1.37, J2.37, U2.5 (A3)
IN_{2}: J1.38, J2.38, U2.6 (A4)
LIMIT_X1_NEG: J1.28, J2.28, U1.4 (A2)
LIMIT_X1_POS: J1.27, J2.27, U1.3 (A1)
LIMIT_X2_NEG: J1.30, J2.30, U1.6 (A4)
LIMIT_X2_POS: J1.29, J2.29, U1.5 (A3)
LIMIT_Y_NEG: J1.32, J2.32, U1.8 (A6)
LIMIT_Y_POS: J1.31, J2.31, U1.7 (A5)
LIMIT_Z_NEG: J1.34, J2.34, U1.10 (A8)
LIMIT_Z_POS: J1.33, J2.33, U1.9 (A7)
OE_{a}: U3.22 (~OE), U5.22 (~OE)
OE_{b}: U4.22 (~OE), U6.22 (~OE)
OUT_{0}_{a}: J1.24, U5.19 (B3)
OUT_{0}_{b}: J2.24, U6.19 (B3)
OUT_{0}_{c}: U5.5 (A3), U6.5 (A3)
OUT_{1}_{a}: J1.25, U5.20 (B2)
OUT_{1}_{b}: J2.25, U6.20 (B2)
OUT_{1}_{c}: U5.4 (A2), U6.4 (A2)
OUT_{2}_{a}: J1.26, U5.21 (B1)
OUT_{2}_{b}: J2.26, U6.21 (B1)
OUT_{2}_{c}: U5.3 (A1), U6.3 (A1)
PROBE: J1.35, J2.35, U2.3 (A1)
SPINDLE_ENABLE_{a}: J1.21, U5.16 (B6)
SPINDLE_ENABLE_{b}: J2.21, U6.16 (B6)
SPINDLE_ENABLE_{c}: U5.8 (A6), U6.8 (A6)
SPINDLE_PWM_{a}: J1.23, U5.18 (B4)
SPINDLE_PWM_{b}: J2.23, U6.18 (B4)
SPINDLE_PWM_{c}: U5.6 (A4), U6.6 (A4)
STEPPER_ENABLE_{a}: J1.22, U5.17 (B5)
STEPPER_ENABLE_{b}: J2.22, U6.17 (B5)
STEPPER_ENABLE_{c}: U5.7 (A5), U6.7 (A5)
STEPPER_X1_DIR_{a}: J1.14, U3.15 (B7)
STEPPER_X1_DIR_{b}: J2.14, U4.15 (B7)
STEPPER_X1_DIR_{c}: U3.9 (A7), U4.9 (A7)
STEPPER_X1_STEP_{a}: J1.13, U3.14 (B8)
STEPPER_X1_STEP_{b}: J2.13, U4.14 (B8)
STEPPER_X1_STEP_{c}: U3.10 (A8), U4.10 (A8)
STEPPER_X2_DIR_{a}: J1.16, U3.17 (B5)
STEPPER_X2_DIR_{b}: J2.16, U4.17 (B5)
STEPPER_X2_DIR_{c}: U3.7 (A5), U4.7 (A5)
STEPPER_X2_STEP_{a}: J1.15, U3.16 (B6)
STEPPER_X2_STEP_{b}: J2.15, U4.16 (B6)
STEPPER_X2_STEP_{c}: U3.8 (A6), U4.8 (A6)
STEPPER_Y_DIR_{a}: J1.18, U3.19 (B3)
STEPPER_Y_DIR_{b}: J2.18, U4.19 (B3)
STEPPER_Y_DIR_{c}: U3.5 (A3), U4.5 (A3)
STEPPER_Y_STEP_{a}: J1.17, U3.18 (B4)
STEPPER_Y_STEP_{b}: J2.17, U4.18 (B4)
STEPPER_Y_STEP_{c}: U3.6 (A4), U4.6 (A4)
STEPPER_Z_DIR_{a}: J1.20, U3.21 (B1)
STEPPER_Z_DIR_{b}: J2.20, U4.21 (B1)
STEPPER_Z_DIR_{c}: U3.3 (A1), U4.3 (A1)
STEPPER_Z_STEP_{a}: J1.19, U3.20 (B2)
STEPPER_Z_STEP_{b}: J2.19, U4.20 (B2)
STEPPER_Z_STEP_{c}: U3.4 (A2), U4.4 (A2)

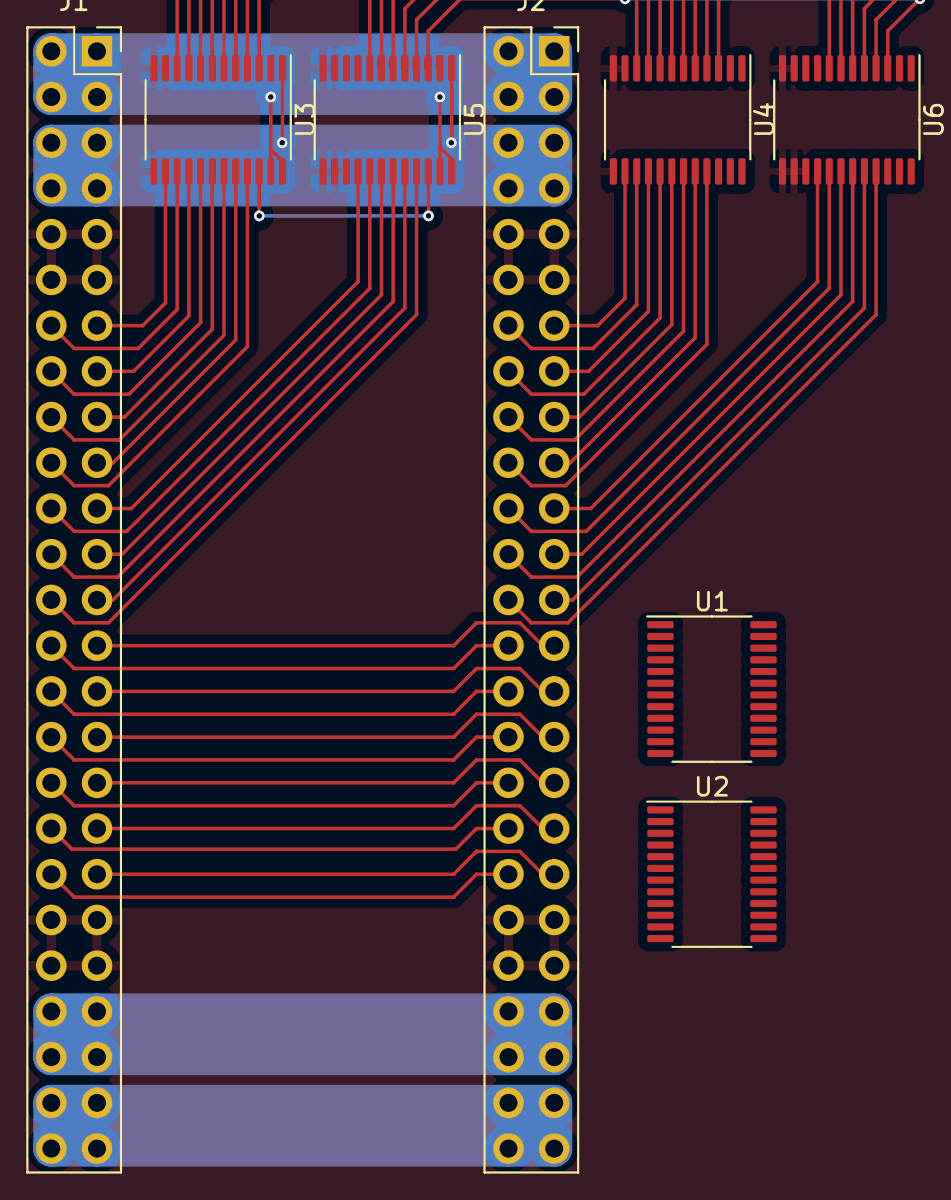
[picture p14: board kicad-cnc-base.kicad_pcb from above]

Board: 2 copper layers, 8 parts (0 on the bottom side), 59 nets.

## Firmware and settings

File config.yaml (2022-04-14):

name: JDCNC
board: unknown

i2so:
  bck_pin: gpio.22
  data_pin: gpio.21
  ws_pin: gpio.17

# kinematics:
#   Cartesian:

stepping:
  engine: I2S_STREAM
  idle_ms: 250
  pulse_us: 4
  dir_delay_us: 1
  disable_delay_us: 0

axes:
  shared_stepper_disable_pin: I2SO.8
  x:
    steps_per_mm: 200.000
    max_rate_mm_per_min: 1000.000
    acceleration_mm_per_sec2: 200.000
    max_travel_mm: 300.000
    soft_limits: false
    motor0:
      limit_neg_pin: gpio.39:low
      limit_pos_pin: gpio.36:low
      hard_limits: true
      standard_stepper:
        direction_pin: I2SO.0
        step_pin: I2SO.1
        disable_pin: NO_PIN
    motor1:
      limit_neg_pin: gpio.35:low
      limit_pos_pin: gpio.34:low
      hard_limits: true
      standard_stepper:
        direction_pin: I2SO.2
        step_pin: I2SO.3
    homing:
      cycle: 2
  y:
    steps_per_mm: 200.000
    max_rate_mm_per_min: 1000.000
    acceleration_mm_per_sec2: 200.000
    max_travel_mm: 300.000
    soft_limits: false
    motor0:
      limit_neg_pin: gpio.33:low
      limit_pos_pin: gpio.32:low
      hard_limits: true
      standard_stepper:
        direction_pin: I2SO.4
        step_pin: I2SO.5
    homing:
      cycle: 2
  z:
    steps_per_mm: 200.000
    max_rate_mm_per_min: 1000.000
    acceleration_mm_per_sec2: 200.000
    max_travel_mm: 300.000
    soft_limits: false
    motor0:
      limit_neg_pin: gpio.26:low
      limit_pos_pin: gpio.25:low
      hard_limits: true
      standard_stepper:
        direction_pin: I2SO.6
        step_pin: I2SO.7
    homing:
      cycle: 1

spi:
  miso_pin: gpio.19
  mosi_pin: gpio.23
  sck_pin: gpio.18

sdcard:
  cs_pin: gpio.5

# control:
#   reset_pin: gpio.34:low:pu
#   feed_hold_pin: gpio.36:low:pu
#   cycle_start_pin: gpio.39:low:pu

coolant:
  delay_ms: 1000.000

probe:
  pin: gpio.27:low
  check_mode_start: true

PWM:
  pwm_hz: 5000
  direction_pin: NO_PIN
  output_pin: gpio.2
  enable_pin: I2SO.14
  disable_with_s0: false
  s0_with_disable: true
  spinup_ms: 0
  spindown_ms: 0
  tool_num: 0
  speed_map: 0=0.000% 10000=100.000%

macros:
  startup_line0: 
  startup_line1: 
  macro0: 
  macro1: 
  macro2: 
  macro3: 

start:
  must_home: true
  check_limits: true
  deactivate_parking: false

user_outputs:
arc_tolerance_mm: 0.002
junction_deviation_mm: 0.010
verbose_errors: false
report_inches: false
enable_parking_override_control: false
use_line_numbers: false 

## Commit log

2022-03-19 added kicad files
    [CNC.kicad_pcb, CNC.kicad_sch]
2022-03-21 started with the base pcb
    [CNC.kicad_pcb, CNC.kicad_sch, kicad-cnc-base.kicad_pcb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]
2022-03-30 updated boards
    [kicad-cnc-connectors.kicad_pcb, kicad-cnc-connectors.kicad_sch, kicad-cnc-esp32.kicad_pcb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]
2022-04-08 updated PCBs
    [kicad-cnc-connectors.kicad_pcb, kicad-cnc-connectors.kicad_sch, kicad-cnc-esp32.kicad_pcb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]
2022-08-27 Added halter
    [Endschalter-Halter.FCStd]
2022-08-27 updated kicad-cnc-esp32
    [kicad-cnc-esp32.kicad_pcb]
